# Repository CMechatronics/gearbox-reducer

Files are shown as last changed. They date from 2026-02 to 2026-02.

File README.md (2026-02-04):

# Industrial Gearbox Speed Reducer

## Overview
This project presents the **design and analysis of an industrial spur gear speed reducer** intended for continuous operation in an automated system.  
The gearbox is designed to reduce motor speed while increasing output torque, ensuring safe and reliable operation.

  ## Technical Specifications
- **Input power:** 7.5 HP  
- **Input speed:** 1440 rpm  
- **Transmission ratio:** i = 2.034 : 1  
- **Output speed:** ≈ 708 rpm  
- **Output torque:** 7.5 kgf·m  
- **Gear type:** Spur gears (straight teeth)  
- **Safety factor:** 3  
- **Lubrication:** Oil bath  
- **Expected service life:**  
  15 years – 300 working days/year – 16 h/day

## Design Scope
The project includes:
- Mechanical design of shafts, gears, housing, and auxiliary components  
- Strength and fatigue calculations for:
  - Gears  
  - Shafts  
  - Keys  
  - Bearings  
- Selection of standard components (bearings, seals, fasteners)  
- Compliance with applicable industrial and safety regulations  
- Manufacturing-oriented drawings and bill of materials  

## Repository Structure
- **/docs** – Design report, calculations, specifications, and budget  
- **/drawings** – Assembly and part drawings  
- **/cad** – 3D CAD models (STEP and native files)  
- **/analysis** – Calculation breakdown by component  
- **/references** – Standards and technical references  

## Tools & Standards
- CAD modeling (mechanical design)  
- Analytical calculations based on mechanical design theory  
- Reference to UNE / EN industrial standards where applicable  

## Author
Carlos López Jiménez  
Industrial Mechatronics – Mechanical Design Project  

## Disclaimer
This repository contains an **engineering design project** developed for technical and educational purposes.  
It is not intended for direct industrial manufacturing without further validation.

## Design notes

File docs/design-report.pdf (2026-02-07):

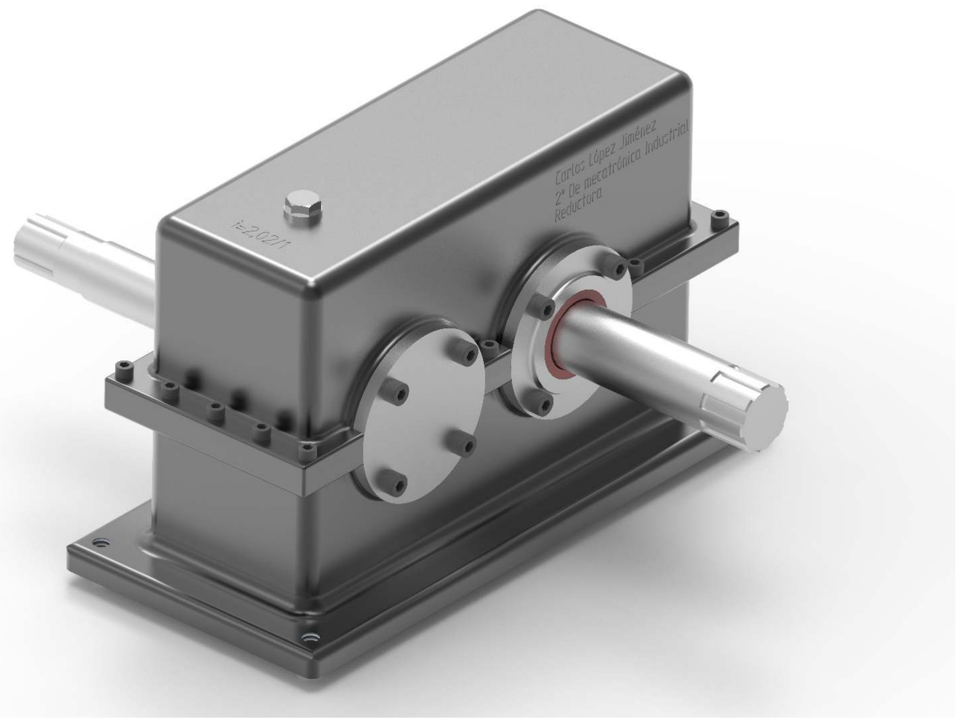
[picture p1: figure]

# PROYECTO REDUCTORA

### DOCUMENTO COMPLETO

CARLOS LÓPEZ JIMÉNEZ
2º DE MECATRÓNICA INDUSTRIAL Salesianos San Ignacio Cádiz

## 21 DE FEBRERO DE 2022

PROYECTO REDUCTORA | 21 DE FEBRERO DE 2022
CARLOS LÓPEZ JIMÉNEZ | 1

Índice general

Memoria del proyecto | 2
Presupuesto | 15
Pliego de condiciones | 48
Planos | 62
Anexo Cálculos | 76

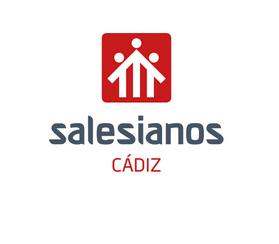
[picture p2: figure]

CARLOS LÓPEZ JIMÉNEZ 2

# Proyecto Reductora de velocidad por engranajes

2º de Mecatrónica Industrial.

# Documento Nº1:

# Memoria del proyecto

Código PR-1

Autor: Carlos López Jiménez Fecha: 21/02/2022

CARLOS LÓPEZ JIMÉNEZ 3

# Índice

2.1.3.1.1 Reducción de velocidad del motor eléctrico mediante variadores de frecuencia. . 4

### 2.1.3.1.2. Reducción de velocidad del motor mediante reductora de velocidad de

### 2.1.3.1.3 Reducción de velocidad del motor mediante reductora de velocidad de tornillo

CARLOS LÓPEZ JIMÉNEZ 4

2.1Principios del documento

Código identificativo: PR-1

2.1.1 Antecendentes del proyecto.

El peticionario José Fuentes Macías con C.I.F. nº: B-12.432.654, y domicilio social en Avenida de la corte 43, 2º izquierda de la localidad de Marbella, Málaga. Posee en Avenida del Polígono Nave 32 de la localidad de Rota, Cádiz, una nave o local donde pretende instalar una actividad dedicada a automatizar la gestión de artículos / Paletizador de velocidad estable.

Se redacta el presente proyecto por el Ingeniero Mecatrónico, Javier González, colegiado en el Colegio oficial de Ingenieros Técnicos Industriales de Aragón con el número 1287.

2.1.2 Objeto del presente proyecto.

Se pretende con este proyecto describir la máquina que desea realizar, justificando y valorando cada una de las partes que componen esta máquina, a fin de recabar de los organismos competentes las oportunas autorizaciones que permitan su legalización y puesta en marcha. La finalidad de dicho proyecto se resume en reducir la velocidad de entrada del brazo mecánico “n” veces para que este trabaje a una adecuada velocidad sin producir riesgos.

2.1.3 Soluciones adoptadas.

2.1.3.1 Soluciones alternativas.

Las soluciones alternativas a las necesidades del cliente son las siguientes:

1. Reducción de velocidad del motor eléctrico mediante variadores de frecuencia.

### 2. Reducción de velocidad del motor mediante reductora de velocidad de

engranajes rectos.

### 3. Reducción de velocidad del motor mediante reductora de velocidad de tornillo

sin fin y corona.
4. Reducción de velocidad del motor mediante reductores planetarios.

2.1.3.1.1 Reducción de velocidad del motor eléctrico mediante variadores de frecuencia.

Descripción del elemento:

CARLOS LÓPEZ JIMÉNEZ 5

Este elemento varía la velocidad gracias a la tecnología electrónica, variando la frecuencia suministrada al motor se puede conseguir que este varíe de velocidad.

La reducción de velocidad del motor por este método puede llegar a ser acertada si el coste de la instalación de este elemento fuera el de un variador de gama baja, es decir en torno a unos 100-500 euros.
La causa de no elegir esta opción es por el simple hecho de que el consumo para el que está diseñado este no es superior al demandado por ello el variador terminaría dañado. Esta potencia que necesitamos es debido a la gran carga que se le quiere dar al paletizador.

Coste económico:

Las opciones de gama alta solucionarían el problema del consumo, pero no el del coste ya que estos rondan sobre los 1600 – 3000 Euros.

Límite tecnológico:

Esta opción como límite tecnológico tiene el problema de que la red eléctrica debe ser cuidada, existe el problema de la generación de ruido por las conmutaciones de los transistores del variador, por ello en este tipo de instalaciones se debe instalar un filtro para no perturbar la señal eléctrica de las demás redes, esto trae los siguientes problemas:

- Mantenimiento de la red eléctrica.
- Instalación del cuadro general de mando y protección dedicado al motor y a su variador.
- Posibles perturbaciones eléctricas en la instalación del emplazamiento e incluso llegando a poder a afectar a otros emplazamientos.
- Costes de instalación caros (filtros, adecuación de instalación del circuito para el motor y el variador).

Como oportunidades para este elemento tenemos las siguientes:

- Puede ser una buena oportunidad para realizar una correcta instalación eléctrica de la nave.
- Una vez realizado los cambios el variador puede limitar el posible exceso de velocidad del motor.
- Los variadores de alta gama protegen a los motores de una forma eficiente.
- Ahorro del consumo del motor entorno a un 20-70%.

Como impacto visual o estético y medioambiental:

La instalación debe ser adecuada y deberá estudiarse la manera de colocar el subcuadro de protección para este instrumento y para la línea trifásica del motor. Por

CARLOS LÓPEZ JIMÉNEZ 6

su reducción de consumo mejora el impacto medioambiental que hubiera generado sin el variador.

Según lo permitido por las administraciones y normativas legales este instrumento es valido para las instalaciones dentro de España según la directiva de la UE 2011/65/UE y 2015/863.

2.1.3.1.2 Reducción de velocidad del motor mediante reductora de velocidad de engranajes rectos.
Descripción del elemento:

La reductora de velocidad de engranajes rectos está formada por pares de ruedas que pueden ser de cualquier tipo, es decir, de dientes rectos, helicoidales, grupos cónicos, etc...

Coste económico:

El coste económico de este tipo de reductores de velocidad puede llegar a ser entre los 1000-1500 euros, en esto se tiene en cuenta la fabricación de estos ya que es para una relación de transmisión personalizada para así poder con la carga que se le dé al paletizador

Límite tecnológico:

En este aspecto tenemos un claro límite en el par o torque, los engranajes, los árboles y las chavetas serán los elementos claramente recibirán los esfuerzos demandados, por ello hay que tener muy claro cual va a ser la masa máxima a soportar con un límite de seguridad. Por otra parte, se enfrentan a otros problemas como pueden ser:

- Mantenimiento de la reductora (revisión del aceite, revisión de las ruedas, árboles y chavetas).
- Limitaciones de carga (estudiar las cargas).
- Tener en cuenta las condiciones del ambiente (temperatura, humedad…).
- Fabricación de piezas (tiempos de espera de la fabricación hasta obtener el producto).
- Revisar el sitio donde se situará la reductora y fijarla (Realizar una buena instalación).
- Si se estropea habría que volver a encargar las piezas, el plazo puede ser largo pudiendo aumentar la criticidad de producción de la empresa por inutilización del paletizador.

Como oportunidades para este elemento tenemos las siguientes:

- Si se diseña bien el conjunto puede tener una gran vida útil.
- Como la lubricación es un tipo de lubricación automática si esta no pierde aceite no será necesario un mantenimiento exhaustivo.

CARLOS LÓPEZ JIMÉNEZ 7

- Tamaño compacto.
- Instalación rápida.
- Ofrece una buena seguridad en la transmisión.

Como impacto visual o estético y medioambiental:

El impacto visual es muy reducido ya que el equipo es compacto. Para reducir el impacto medioambiental del aceite mineral deberá llevarse a contenedores específicos para ello.

Este elemento deberá seguir la norma UNE-EN 13463-6:2005 por la peligrosidad del aceite como fuente de ignición (en su estado gaseoso puede generarse una reacción química con el oxígeno que lo convierta en inflamable).

2.1.3.1.3 Reducción de velocidad del motor mediante reductora de velocidad de tornillo sin fin y corona.
Descripción del elemento:

El mecanismo consiste en un tornillo sinfín montado en el eje motor haciendo girar la corona en el que estará fijado solidariamente el eje de salida, por transmisión de fuerza y movimiento entre estos ejes son capaces de resistir cargas muy elevadas.

Coste económico:

En cuanto al coste económico debemos tener en cuenta que se trata de un elemento que al igual que la reductora deberán de fabricarse las piezas del conjunto, teniendo en cuenta la dificultad de fabricación del tornillo sinfín y que por ello la forma de los dientes de la corona será más compleja que la de los dientes rectos puede llegar a ser más laborioso, por ello los costes podrían ascender a unos 2000-2600 euros.

Límite tecnológico:

Como límite tecnológico tenemos que por lo general no se puede realizar un cambio de entrada de transmisión ya que el sinfín es el que se suele usar para transmitir el movimiento al árbol motriz. Pueden existir otros problemas como:

- Si no se diseña correctamente y aparece un fallo repentino este no podrá ser sustituido con brevedad ya que se deberá fabricar de nuevo
- Una de las principales desventajas del sinfín es el bajo rendimiento que ofrecen estas etapas de reducción, que puede situarse en torno al 15% debido a los altos valores de fuerza de rozamiento y a los esfuerzos axiales asociados.

CARLOS LÓPEZ JIMÉNEZ 8

- El desgaste que sufre el sinfín se produce en las superficies de apoyo las cuales están sometidas a fricción, por ello es necesario que sean altamente resistentes y que estén perfectamente calibrados para que su vida útil sea larga.
- Existe un cierto riesgo de desgaste de los filetes si se produce fricción excesiva en la zona.

Como oportunidades para este elemento tenemos las siguientes:

- Tamaño compacto
- Si se diseña correctamente puede tener una larga vida útil.
- Poco mantenimiento ya que su lubricación es automática.

Como impacto visual o estético y medioambiental:

No perturba la visión estética ya que es un elemento compacto, pero con su aceite mineral se deberá cuidar su correcto reciclado.

Este elemento deberá seguir la norma UNE-EN 13463-6:2005 por la peligrosidad del aceite como fuente de ignición (en su estado gaseoso puede generarse una reacción química con el oxígeno que lo convierta en inflamable).

2.1.3.1.4 Reducción de velocidad del motor mediante reductores planetarios. Descripción del elemento:

Los reductores planetarios se caracterizan por un elevado grado de efectividad y, gracias a su forma de construcción compacta, ofrece una alta densidad de potencia en comparación con otros tipos de construcción de reductores. Especialmente la utilización de una rueda hueca reduce tanto el volumen como la masa de este tipo de reductor.

Coste económico:

Los costes de estos engranajes son muy costosos, el diseño puede llegar a ser complejo y su fabricación también lo es, por ello los costes pueden ascender a los 200-4000 euros si se requiere un buen par de fuerza en torno a los 400 Nm.

Límite tecnológico:

No se pueden hacer más silenciosos, y sin lubricante no podrán funcionar correctamente. Otros inconvenientes pueden ser:

- El engranaje debe ser preciso para asegurar el reparto de la carga

CARLOS LÓPEZ JIMÉNEZ 9

- Las elevadas cargas de los cojinetes pueden provocar un descaste prematuro en la construcción de muñones.
- Generalmente necesita lubricación con grasa, pero la lubricación de baño en aceite es mejor
- Relación alta de longitud a diámetro cuando se utilizan múltiples etapas (el reductor se vuelve muy largo).
- Alto costo

Como oportunidades para este elemento tenemos las siguientes:

Este se puede útil por su eficiencia, en ese aspecto cumpliría por encima las expectativas, así como su ligereza. También se pueden resaltar las siguientes características:

- Tamaño compacto y bajo peso hasta un 50 % de reducción con el mismo par de torsión
- Densidad de alta potencia
- Vida larga de los engranajes
- Muy preciso
- Etapas modulares, más planetarias pueden ser apiladas.

Como impacto visual o estético y medioambiental:

En este caso este tipo de reductora si crea un impacto visual y puede romper con la estética ya debido a la cantidad de etapas esta reductora termina siendo alargada y ocupando espacio quedando vistoso a simple vista. Hay que tener en cuenta que el aceite deberá ser correctamente reciclado.

Este elemento deberá seguir la norma UNE-EN 13463-6:2005 por la peligrosidad del aceite como fuente de ignición (en su estado gaseoso puede generarse una reacción química con el oxígeno que lo convierta en inflamable).

2.1.3.2 Justificación de la solución adoptada.
Reuniendo las características de las cuatro opciones plantadas se ha llegado a una conclusión de que la mejor opción en términos de calidad es la reductora de velocidad de engranajes rectos.

Comparando esta opción con las demás consideramos que es la mejor opción por las siguientes características que resaltan respecto a los demás:

- Elemento compacto
- Poco vistoso
- Fabricación del conjunto relativamente simple respecto a los demás, exceptuando al variador.

CARLOS LÓPEZ JIMÉNEZ 10

- Si bien es verdad que este tipo de reductora no está pensada para cargas muy grandes el cliente especifica que no es necesario que en ese aspecto resalte tanto como por ejemplo la reductora con sinfín y corona, que si están pensados para esfuerzos muy grandes, concretamente por la función que desempeñará no tendrá que soportar la carga completa de la carga máxima permitida en cuestión
- La instalación es muy sencilla y por ello podemos evitar reducir la cantidad de instalaciones adicionales como ocurre en el caso del variador de frecuencia.
- En tema legislativo no es complejo, es mínimo, como ocurre con el caso del aceite.
- Económicamente se adapta al presupuesto máximo que se permite gastar el cliente.
2.1.4. Reglamentaciones y disposiciones oficiales particulares.
Se redacta el presente proyecto para dar cumplimiento a las siguientes:
- Esta reductora cumple con la directiva europea 94/9/CE (ATEX-100) Real Decreto 400/1996 con temática para aparatos y sistemas de protección para usos en atmósferas explosivas.
- El lugar donde se instalará cumple con la directiva europea 99/92/CE (ATEX-
137) Real Decreto 681/2003 con temática de protección de la seguridad y salud de los trabajadores expuestos a los riegos derivados de la presencia de atmósferas explosivas en el lugar de trabajo.
- Esta reductora no debe instalarse en un emplazamiento en el que el ambiente sea potencialmente explosivo por precaución. Las mezclas de gas explosivas o concentraciones de polvo pueden causar graves daños en combinación con partes calientes en movimiento de los reductores.
- La instalación, conexión, puesta en marcha y tareas de mantenimiento o reparación de los reductores deberán ser efectuadas únicamente por técnicos cualificados.
- Este reductor estándar no puede utilizarse en entornos con una atmósfera potencialmente explosiva. Para dicho uso debe solicitarse la ejecución específica que satisfaga la directiva 94/9/CE (ATEX).
- Este reductor está destinado a ser incorporado y/o ensamblado con otras máquinas o componentes, se considera “componente·, por lo que no puede ponerse en servicio antes de que la máquina a la que se va a incorporar se declare conforme a las disposiciones de la directiva de máquinas 2006/42/CE.
- Real Decreto 786/2001, de 6 de Julio, por el que se aprueba el reglamento de seguridad contra incendios en establecimientos industriales.
- NBE CPI-96 de Protección contra Incendios en los Edificios
- Reglamento de Actividades Molestas, Insalubres, Nocivas y peligrosas (Decreto 241461 de 3/11/61).

CARLOS LÓPEZ JIMÉNEZ 11

- Decreto 297/1995 de 19 de Diciembre (Boja nº3/11-01-96) por el que se aprueba el reglamento de Calificación Ambiental.
- Real Decreto 1435/92 por el que se dictan las disposiciones de aplicación de la directiva del Concejo 89/92/CEE, relativa a la aproximación de las legislaciones de los estados miembros sobre máquinas.

2.1.4.1 Bibliografía
Normativas usadas para la reductora:

http://rodytrans.es/wp-content/uploads/Manual-instrucción-montaje-engranajes.pdf

http://www.atmosferasexplosivas.com/index.php/normativaatex

Reductores de velocidad:

https://clr.es/blog/es/reductores-velocidad-funcionamiento/

https://www.nord.com/es/productos/reductores-industriales/motorreductores_industriales.jsp;jsessionid=DECCDB9545F884C51F9605EBA068EC99?missing=/cms/es/product_catalogue/industrial_gear_unit/pgop_industrial_gear_unit_1.jsp

Variadores de frecuencia:

https://new.abb.com/drives/es/que-es-un-variador

2.1.4.2 Plan de gestión de la calidad aplicado durante la redacción del proyecto. Se han asegurado los procesos de calidad correspondientes a la fabricación de la reductora estos son los descritos a continuación:

- Planificación de la fabricación y definir procesos.
- Planificación del montaje
- Distribución del trabajo.
- Evaluación de riesgos.
- Medidas de prevención de riesgos.
- Hoja de recopilación de datos
- Histograma
- Diagrama de dispersión
- Gráficos de control
- Mantenimiento productivo total (TPM)

CARLOS LÓPEZ JIMÉNEZ 12

2.1.5 Requisitos de diseño
En este proyecto el cliente facilita los datos de partida requeridos que son los descritos en la siguiente tabla:

Condiciones expuestas por el cliente
P (CV) | 7,5
n (rpm) | 1440
Par de salida (Kgf·m) | 7,5
Factor de seguridad (S) | 3
Vida útil | 15 años, 300 días laborables y 16 h/día de trabajo

El cliente solicita una reductora de engranajes de dientes rectos, en el de base tenemos que la potencia en Caballos de Vapor es de 7,5 a su vez determina que la velocidad del motor en revoluciones por minuto será de 1440.
Le preocupa que el par de salida sea inferior a 7,5 y superior a 8 Kilogramos fuerza por metro.
Determinamos un factor de seguridad de 3 para los elementos que serán sometidos a esfuerzos.

Al cliente le preocupa que la vida útil sea de la reductora sea inferior a 15 años, 300 días laborables y 16 h/día de trabajo.

2.1.5.1 Legislación, reglamentación y normativas aplicables.
Estas se han señalado en el apartado de 2.1.4 Normas y referencias.

2.1.5.2 Estudios realizados encaminados a la definición de la solución adoptada.
En la reductora elegida según el apartado 2.1.3 Solución adoptada, se refleja el por qué se ha decidido realizar el diseño de la reductora en concreto.
En este apartado se señalarán las decisiones de construcción de elementos adoptadas.

En la mayoría de los apartados siguientes se reflejó la justificación de elección en el Anexo de Cálculos, por ello los apartados que no estén explicados en dicho anexo serán justificados aquí.

2.1.5.2.1 Árboles de transmisión
En esta reductora se ha elegido reducción de velocidad por 2 pares de ruedas, lo que conlleva a que existan 2 árboles, uno conductor y otro conducido.

En el Anexo de Cálculos apartado 1.4 se refleja la elección de los árboles de diámetro

### 35 y 40 según el momento flector dado en cada uno de ellos y considerando el tamaño

más reducido posible para obtener un tamaño compacto de la reductora.

CARLOS LÓPEZ JIMÉNEZ 13

2.1.5.2.2 Ruedas dentadas.
El piñón y la corona son dos elementos esenciales, se decidió una transmisión con ruedas de dientes rectos en el apartado 2.1.3 Solución adoptada. Se ha determinado las dimensiones tendiendo a reducir el volumen de estas al máximo posible atendiendo también a obtener el par de fuerza acordado. Los detalles aparecerán en el Anexo de Cálculos apartado 1.3

2.1.5.2.3 Chavetas.
Las chavetas elegidas han sido elegidas según el esfuerzo calculado al que se verán sometidas, a partir de estos datos se ha elegido una longitud de chaveta acorde a la superficie del chavetero siendo esta de largo inferior a la longitud de dicho chavetero, de este modo se ha atendido al catálogo del fabricante norelem mirando que cumpla las expectativas calculadas.

Más información referenciada en Anexo de Cálculos apartado 1.5

2.1.5.2.4 Rodamientos.
Los rodamientos para carga radial son elegidos según la carga a las que son sometidos, se ha escogido al fabricante de rodamientos SKF donde en el anexo de cálculos en los que se puede observar que según la carga que se ha determinado estos son aptos para este conjunto.

Más información referenciada en el Anexo de Cálculos apartado 1.6

2.1.5.2.5 Retenes
Los retenes elegidos han sido unos NBR (caucho de Acrilo nitrilo butadieno), en dimensiones nos hemos ceñido a la menor dimensión posible de su diámetro exterior, su diámetro interior atendiendo a el árbol de transmisión respectivo.

Elección aclarada en el Anexo de Cálculos apartado 1.8

2.1.5.2.6 Elementos de montaje.
Todos los elementos de montaje tales como la carcasa, tapetas, casquillos y tornillos han sido elegidos con el enfoque de obtener una reductora lo más compacta posible, por ello se han determinado dimensiones lo más reducidas posibles pero que también aporten un acople entre estos.

Más información en el Anexo de Cálculos apartado 1.9 donde se aclara el diseño geométrico de los distintos elementos constructivos.

2.1.5.2.7 Lubricación
La lubricación es un factor muy importante donde exista rozamiento entre piezas, se puede alargar la vida útil de este, así como el rendimiento seleccionando un buen lubricante.

Se ha optado por realizar un baño en aceite ya que es el más adecuado para este caso ya que las propias ruedas serán la que se impregnen continuamente de aceite

CARLOS LÓPEZ JIMÉNEZ 14

teniendo una lubricación óptima en todo momento. En el Anexo de Cálculos apartado 1.7.

2.1.6 Resultados finales.
Como se ha ido viendo según los pasos dados hemos obtenido una reductora de velocidad por 2 pares de engranajes rectos cuales son fijados gracias a sus chaveteros que se acoplarán con los chaveteros de los árboles de transmisión, el movimiento axial será limitado gracias a los casquillos separadores que harán tope con los rodamientos y estos a su vez con la tapeta que estará fijada a la carcasa. Esta reductora dispondrá de un tapón de llenado y de vaciado para obtener una lubricación automática, en pocas palabras obtendremos un reductor de velocidad compacto y simple ya que solo existe una sola etapa, este podrá ser fijado gracias a los orificios pasantes que se han facilitado en cada esquina de la reductora.

La transmisión de movimiento entre el motor y el árbol de transmisión se realizará mediante un acople de ejes con acanaladuras.

2.1.7 Planificación.
En este proceso de fabricación de la reductora se han tenido diferentes etapas, se definirán a continuación:
- Etapa de replanteo y planificación: Se examinaron los datos solicitados por el cliente desde el departamento de administración, se pasaron los datos al departamento técnico que estudió las peticiones del cliente y en este se planificó la forma de en la que se iba a hacer.
- Etapa de estudio y desarrollo: Se finalizó el estudio completo de las posibilidades que se plantearon y se comenzó el desarrollo una vez establecido una comunicación con el cliente. Se desarrollaron los cálculos necesarios y los planos de los elementos una vez determinados.
- Etapa de estimación de tiempo de entrega y fabricación: Una vez terminado el estudio y la realización de planos se estimó el tiempo de fabricación, empaquetado y envío y se realizó un presupuesto completo, se le pidió al cliente una confirmación de este, una vez recibida la señal se inició la fabricación con las fechas de entrega asignadas.
2.1.8. Orden de prioridad entre los documentos básicos.
Orden de documentos básicos:

1 Planos.
2 Pliego de condiciones.
3 Presupuesto.
4 Memoria.

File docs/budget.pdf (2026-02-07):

PROYECTO REDUCTORA | 21 DE FEBRERO DE 2022


CARLOS LÓPEZ JIMÉNEZ | 15

# Proyecto Reductora de velocidad por engranajes

2º de Mecatrónica Industrial.

# Documento Nº4:

# Presupuesto

Código PR-4

Autor: Carlos López Jiménez Fecha: 21/02/2022

Presupuesto | Reductora
Mediciones | Reductora
Capítulo | 01
Código | Ud | N | Long | Ancho | Altura

Cantidad
Precio Importe

### 01.0 Piñón

Ud Piñón | 1 | 69 | ø 85,25
Total: | 1

### 01.1 Corona

Ud Corona | 1 | 69 | ø 167,75
Total: | 1

### 01.2.0 Árbol de transmisión de entrada

Ud Árbol de entrada | 1 | 267 | ø 35
Total: | 1

### 01.2.1 Árbole de transmisión de salida

Ud Árbol de salida | 1 | 267 | ø 40
Total: | 1

### 01.3.1 Tapeta árbol de entrada

Ud Tapeta árbol de entrada | 1 | 16 ø 100
Total: | 1

### 01.3.2 Tapeta árbol de entrada ciega

Ud Tapeta árbol de entrada ciega | 1 | 13 ø 100
Total: | 1

### 01.3.3 Tapeta de árbol de salida

Ud Tapeta árbol de salida | 1 | 16 ø 100
Total: | 1

Subcapítulo

Subcapítulo

Reductora

Descripción

Subcapítulo

Subcapítulo

Subcapítulo

Ruedas dentadas

Árboles de transmisión

Tapetas

Subcapítulo

Subcapítulo

Carlos López Jiménez | 21/02/2021 | Página 1

Mediciones | Reductora
Capítulo | 01
Código | Ud | N | Long | Ancho | Altura

Cantidad
Precio Importe

Reductora

Descripción

### 01.3.4 Tapeta árbol de salida ciega

Ud Tapeta árbol de salida ciega | 1 | 13 ø 100
Total: | 1

### 01.4.0 Casquillos separadores árbol de entrada

Ud Casquillo separador árbol de entrada | 2 | 15 ø 45
Total: | 2

### 01.4.1 Casquillos separadores árbol de salida

Ud Casquillo separador árbol de salida | 2 | 15 ø 50
Total: | 2

### 01.5.0 Caja de la reductora parte inferior

Ud Caja de de reductora parte inferior | 1 | 380 | 179 110,5
Total: | 1

### 01.5.1 Caja de la reductora parte superior

Ud Caja de reductora parte superior | 1 | 358 | 117 106,5
Total: | 1

### 01.6.0 Tornillería

Ud Tornillo M6 x 18 | 14 | 18 | | ø 6
Ud Tornillo M8 x 16 | 16 | 16 | | ø 8
Ud Tornillo tapón M16 x 12 | 2 | 12 | | ø 16
Total: | 32

### 01.6.1 Elementos de arrastre

Ud Lengüeta plana tipo A 12x8x56 | 1 | 12 | 56 | 8
Ud Lengüeta plana tipo A 10x8x56 | 1 | 10 | 56 | 8

Subcapítulo

Subcapítulo

Elementos que no se tienen que fabricar

Subcapítulo

Subcapítulo

Subcapítulo

Casquillos

Caja

Subcapítulo

Subcapítulo

Carlos López Jiménez | 21/02/2021 | Página 2

Mediciones | Reductora
Capítulo | 01
Código | Ud | N | Long | Ancho | Altura

Cantidad
Precio Importe

Reductora

Descripción

Total: 2

### 01.6.2 Rodamientos

Ud Rodamientos rígidos de bolas 16007 | 2 | 9 ø 62
Ud Rodamientos rígidos de bolas 16008 | 2 | 9 ø 68
Total: | 4

### 01.6.3 Retenes

Ud Retén NBR 35x45x7 | 2
Ud Retén NBR 40x52x7 | 2
Total: | 4

### 01.6.4 Elementos consumibles

l | 2,85
gr | 110

2,85

110

### 01.7.0 Montaje

Ud Montaje | 1
Total: | 1

Subcapítulo

Montaje

Sellador para estanqueidad de uniones

Lubricante API GL1

Total litros:

Total gramos:

Subcapítulo

Subcapítulo

Subcapítulo

Carlos López Jiménez | 21/02/2021 | Página 3

Procesos descompuestos | Reductora
Capítulo | 01
Código | Ud

N

Tiempo total
de la
operación

Precio
unidad Importe

### 01.1.0 Piñón

Ud

Kg | Cilindro Acero 37Cr4 | 1 | 5 | | 7,50 € | 37,50 €
minutos | Estudiar plano y hoja de proceso | 1 | 2 | 2 | 0,33 € | 0,66 €
minutos | Recoger , limpiar y devolver piezas útiles | 3 | 5,11 | 15,33 | 0,33 € | 5,06 €
minutos | Limpieza de la máquina | 1 | 15 | 15 | 0,33 € | 4,95 €
minutos | Puesta a punto ejes X y Z comprobaciones y control | 1 | 4,8 | 4,8 | 0,33 € | 1,58 €
minutos | Coger trozo de material, posicionarlo, centrar a mano y quitar | 1 | 0,7 | 0,7 | 0,33 € | 0,23 €
minutos | Poner ajustar y quitar pinza con soporte cónico autocentrante | 3 | 0,7 | 2,1 | 0,33 € | 0,69 €
minutos | Montar, centrar/ ajustar y desmontar herramienta o portaherramienta de acabado | 1 | 0,85 | 0,85 | 0,33 € | 0,28 €
minutos | Montar herramienta en portaherramientas | 1 | 0,25 | 0,25 | 0,33 € | 0,08 €
minutos | Ajustar altura de la cuchilla | 1 | 0,42 | 0,42 | 0,33 € | 0,14 €
minutos | Comprobar alineación puntros eje y contracabezal con barra de prueba y comparador centesimal | 2 | 5 | 10 | 0,33 € | 3,31 €
minutos | Cambio de herramienta | 1 | 0,35 | 0,35 | 0,33 € | 0,12 €
minutos | Colocación del carro en posición de trabajo, ajustar pasada y aproximar herramienta a la pieza | 6 | 0,55 | 3,3 | 0,33 € | 1,09 €
minutos | Primera pasada de prueba, medir y volver a posición de trabajo | 2 | 0,15 | 0,3 | 0,33 € | 0,10 €
minutos | Sacar y volver a introducir la herramienta para eliminar viruta | 6 | 0,15 | 0,9 | 0,33 € | 0,30 €
minutos | Retirar carro, ajustar pasada con el nonio y volver a posición de trabajo | 6 | 0,55 | 3,3 | 0,33 € | 1,09 €
minutos | Comprobación de medidas | 2 | 0,3 | 0,6 | 0,33 € | 0,20 €
minutos | Comprobación medida final | 1 | 0,3 | 0,3 | 0,33 € | 0,10 €
minutos | Invertir pieza amarrada en plato universal | 2 | 0,3 | 0,6 | 0,33 € | 0,20 €

Reductora

Descripción

Cantidad (Kg o
min)

Ruedas dentadas

Fabricación de piñón según planos al que se le hará un chavetero acorde a la lengüeta designada, las operaciones se realizarán mediante fresas para el mecanizado y tallado de dientes. Material empleado: 37Cr4

Subcapítulo

Carlos López Jiménez | 21/02/2021 | 25

Capítulo | 01
Código | Ud

N

Tiempo total
de la
operación

Precio
unidad Importe

Reductora

Descripción

Cantidad (Kg o
min)
minutos | Colocación de fresa | 1 | 0,55 | 0,55 | 0,33 € | 0,18 €
minutos | Colocación de rueda dentada en el plato universal | 1 | 0,4 | 0,4 | 0,33 € | 0,13 €
minutos | Ajuste de aparato divisor | 1 | 5 | 5 | 0,33 € | 1,65 €
minutos | Tallado de un diente | 29 | 1,5 | 43,5 | 0,33 € | 14,39 €
minutos | Taladrado ø35 H7 | 1 | 4 | 4 | 0,33 € | 1,32 €
minutos | Fresado del chavetero 69 mm longitud y 3,3 mm de t2 | 1 | 1,2 | 1,2 | 0,33 € | 0,40 €
minutos | Refrentado de 1 mm para llegar a 15 mm, hacer en las dos caras | 30 | 0,5 | 15 | 0,33 € | 4,96 €
minutos | Cilindrado de 1mm para vaciado de rueda desde ø62 a ø45 (17 mm de cilindrado) hacer en las dos caras | 34 | 0,4 | 13,6 | 0,33 € | 4,50 €
Tiempo total invertido en minutos | 144,35
Ud | horas
| 2,406
MO01 | horas | Oficial de 1ª Ferralista | 1 | 19,85 € | 47,76 €
| | | Subtotal partida subcapítulo 01.1 (CD) | | 85,26 €
| | | %Costes Indirectos (CI) | | 7%
| | | Total partida subcapítulo 01.1 | | 91,22 €
| | 01.1.1 Corona
| Ud
Kg | Cilindro Acero 37Cr4 | 1 | 20 | | 7,50 € | 150,00 €
minutos | Estudiar plano y hoja de proceso | 1 | 2 | 2 | 0,33 € | 0,66 €
minutos | Recoger , limpiar y devolver piezas útiles | 3 | 5,11 | 15,33 | 0,33 € | 5,06 €
minutos | Limpieza de la máquina | 1 | 15 | 15 | 0,33 € | 4,95 €
minutos | Puesta a punto ejes X y Z comprobaciones y control | 1 | 4,8 | 4,8 | 0,33 € | 1,58 €
minutos | Coger trozo de material, posicionarlo, centrar a mano y quitar | 1 | 0,7 | 0,7 | 0,33 € | 0,23 €
minutos | Poner ajustar y quitar pinza con soporte cónico autocentrante | 3 | 0,7 | 2,1 | 0,33 € | 0,69 €
minutos | Montar, centrar/ ajustar y desmontar herramienta o portaherramienta de acabado | 1 | 0,85 | 0,85 | 0,33 € | 0,28 €
minutos | Montar herramienta en portaherramientas | 1 | 0,25 | 0,25 | 0,33 € | 0,08 €
minutos | | 1 | 0,42 | 0,42 | 0,33 € | 0,14 € Ajustar altura de la cuchilla

Fabricación de piñón según planos al que se le hará un chavetero acorde a la lengüeta designada, las operaciones se realizarán mediante fresas para el mecanizado y tallado de dientes. Material empleado: 37Cr4

Subcapítulo

Capítulo | 01
Código | Ud

N

Tiempo total
de la
operación

Precio
unidad Importe

Reductora

Descripción

Cantidad (Kg o
min)
minutos | Comprobar alineación puntros eje y contracabezal con barra de prueba y comparador centesimal | 2 | 5 | 10 | 0,33 € | 3,31 €
minutos | Cambio de herramienta | 1 | 0,35 | 0,35 | 0,33 € | 0,12 €
minutos | Colocación del carro en posición de trabajo, ajustar pasada y aproximar herramienta a la pieza | 6 | 0,55 | 3,3 | 0,33 € | 1,09 €
minutos | Primera pasada de prueba, medir y volver a posición de trabajo | 2 | 0,15 | 0,3 | 0,33 € | 0,10 €
minutos | Sacar y volver a introducir la herramienta para eliminar viruta | 6 | 0,15 | 0,9 | 0,33 € | 0,30 €
minutos | Retirar carro, ajustar pasada con el nonio y volver a posición de trabajo | 6 | 0,55 | 3,3 | 0,33 € | 1,09 €
minutos | Comprobación de medidas | 2 | 0,3 | 0,6 | 0,33 € | 0,20 €
minutos | Comprobación medida final | 1 | 0,3 | 0,3 | 0,33 € | 0,10 €
minutos | Invertir pieza amarrada en plato universal | 2 | 0,3 | 0,6 | 0,33 € | 0,20 €
minutos | Colocación de fresa | 1 | 0,55 | 0,55 | 0,33 € | 0,18 €
minutos | Colocación de rueda dentada en el plato universal | 1 | 0,4 | 0,4 | 0,33 € | 0,13 €
minutos | Ajuste de aparato divisor | 1 | 5 | 5 | 0,33 € | 1,65 €
minutos | Tallado de un diente | 59 | 1,5 | 88,5 | 0,33 € | 29,28 €
minutos | Taladrado ø40 H7 | 1 | 4 | 4 | 0,33 € | 1,32 €
minutos | 3,3 mm de t2 | 1 | 1,2 Fresado del chavetero 69 mm longitud y | 1,2 | 0,33 € | 0,40 €
minutos | hacer en las dos caras | 30 | 0,5 Refrentado de 1 mm para llegar a 15 mm, | 15 | 0,33 € | 4,96 €
minutos | Cilindrado de 1mm para vaciado de rueda desde ø140 a ø50 (90 mm de cilindrado) hacer en las dos caras | 180 | 0,4 | 72 | 0,33 € | 23,82 €
Tiempo total invertido en minutos | 247,75
Ud | horas
| 4,129
MO01 | horas | Oficial de 1ª Ferralista | 1 | 19,85 € | 81,96 €
Subtotal partida subcapítulo 01.1.1 (CD) | 231,96 €
| | | %Costes Indirectos (CI) | | 7%
| | | Total partida subcapítulo 01.1.1
| | | Total partida subcapítulo 01.1 | | 339,43 €

### 01.2.0 Árbol de transmisión de entrada

Ud

Árboles de transmisión

Subcapítulo

Fabricación del árbol de transmisión de entrada de 267 mm de largo, Ø35 h11, fabricación asiento para la lengûeta plana de 10x8x56, achaflanado de extremos del árbol y fabricación en un extremo de nervado de longitud 30 y Ø32. Material empleado: Acero 37CrMo4

248,2014 €

Capítulo | 01
Código | Ud

N

Tiempo total
de la
operación

Precio
unidad Importe

Reductora

Descripción

Cantidad (Kg o
min)
Kg | Cilindro Acero 37CrMo4 | 1 | 3,7 | | 6,70 € | 24,79 €
minutos | Estudiar plano y hoja de proceso | 1 | 2 | 2 | 0,33 € | 0,66 €
minutos | Recoger , limpiar y devolver piezas útiles | 3 | 5,11 | 15,33 | 0,33 € | 5,06 €
minutos | Limpieza de la máquina | 1 | 15 | 15 | 0,33 € | 4,95 €
minutos | Puesta a punto ejes X y Z comprobaciones y control | 1 | 4,8 | 4,8 | 0,33 € | 1,58 €
minutos | Poner ajustar y quitar pinza con soporte cónico autocentrante | 3 | 0,7 | 2,1 | 0,33 € | 0,69 €
minutos | Montar, centrar/ ajustar y desmontar herramienta o portaherramienta de acabado | 1 | 0,85 | 0,85 | 0,33 € | 0,28 €
minutos | Montar herramienta en portaherramientas | 1 | 0,25 | 0,25 | 0,33 € | 0,08 €
minutos | Ajustar altura de la cuchilla | 1 | 0,42 | 0,42 | 0,33 € | 0,14 €
minutos | Comprobar alineación puntros eje y contracabezal con barra de prueba y comparador centesimal | 2 | 5 | 10 | 0,33 € | 3,31 €
minutos | Cambio de herramienta | 1 | 0,35 | 0,35 | 0,33 € | 0,12 €
minutos | Colocación del carro en posición de trabajo, ajustar pasada y aproximar herramienta a la pieza | 6 | 0,55 | 3,3 | 0,33 € | 1,09 €
minutos | Primera pasada de prueba, medir y volver a posición de trabajo | 2 | 0,15 | 0,3 | 0,33 € | 0,10 €
minutos | Sacar y volver a introducir la herramienta para eliminar viruta | 6 | 0,15 | 0,9 | 0,33 € | 0,30 €
minutos | Retirar carro, ajustar pasada con el nonio y volver a posición de trabajo | 6 | 0,55 | 3,3 | 0,33 € | 1,09 €
minutos | Comprobación de medidas | 2 | 0,3 | 0,6 | 0,33 € | 0,20 €
minutos | Comprobación medida final | 1 | 0,3 | 0,3 | 0,33 € | 0,10 €
minutos | Invertir pieza amarrada en plato universal | 2 | 0,3 | 0,6 | 0,33 € | 0,20 €
minutos | Colocación de fresa | 1 | 0,55 | 0,55 | 0,33 € | 0,18 €
minutos | Cilindrado de 1mm al árbol a ø35 h11. ø del cilíndro sin mecanizar ø45, largo del recorrido 267mm | 10 | 0,45 | 4,5 | 0,33 € | 1,49 €
minutos | Cilindrado de 1 mm, para llegar a dejarlo a 30mm longitud y ø28 | 30 | 0,45 | 13,5 | 0,33 € | 4,47 €
minutos | Refrentado de 1mm de caras hasta dejar el árbol a 267, siendo el cilindro a mecanizar de 280 | 13 | 0,5 | 6,5 | 0,33 € | 2,15 €

Capítulo | 01
Código | Ud

N

Tiempo total
de la
operación

Precio
unidad Importe

Reductora

Descripción

Cantidad (Kg o
min)
minutos | Fresado de 1 mm del chavetero 10x8x56 a la profundidad de fresado de 4,7 . | 4,7 | 0,38 | 1,786 | 0,33 € | 0,59 €
minutos | Fresado de 1mm del chavetero 10x8x56, a longitud 56 | 56 | 0,3 | 16,8 | 0,33 € | 5,56 €
minutos | Fresado de una acanaladura a 30 mm de longitud, 6 de ellas a ø28. | 6 | 4 | 24 | 0,33 € | 7,94 €
minutos | Achaflanado 1x45º en una cara, en total 2 caras | 2 | 0,8 | 1,6 | 0,33 € | 0,53 €
Tiempo total invertido en minutos | 129,64
Ud | horas
| 2,161
MO01 | horas | Oficial de 1ª Ferralista | 1 | 19,85 € | 42,89 €
Subtotal partida subcapítulo 01.2. (CD) | 67,68 €
| | | %Costes Indirectos (CI) | | 7%
| | | Total partida subcapítulo 01.2. | | 72,42 €
| | 01.2.1 Árbol de transmisión de salida

Ud

Kg | Cilindro Acero 37CrMo4 | 1 | 4,5 | | 6,70 € | 30,15 €
minutos | Estudiar plano y hoja de proceso | 1 | 2 | 2 | 0,33 € | 0,66 €
minutos | Recoger , limpiar y devolver piezas útiles de medición | 3 | 5,11 | 15,33 | 0,33 € | 5,06 €
minutos | Limpieza de la máquina | 1 | 15 | 15 | 0,33 € | 4,95 €
minutos | Puesta a punto ejes X y Z comprobaciones y control | 1 | 4,8 | 4,8 | 0,33 € | 1,58 €
minutos | Poner ajustar y quitar pinza con soporte cónico autocentrante | 3 | 0,7 | 2,1 | 0,33 € | 0,69 €
minutos | Montar, centrar/ ajustar y desmontar herramienta o portaherramienta de acabado | 1 | 0,85 | 0,85 | 0,33 € | 0,28 €
minutos | Montar herramienta en portaherramientas | 1 | 0,25 | 0,25 | 0,33 € | 0,08 €
minutos | Ajustar altura de la cuchilla | 1 | 0,42 | 0,42 | 0,33 € | 0,14 €
minutos | Comprobar alineación puntros eje y contracabezal con barra de prueba y comparador centesimal | 2 | 5 | 10 | 0,33 € | 3,31 €
minutos | Cambio de herramienta | 1 | 0,35 | 0,35 | 0,33 € | 0,12 €
minutos | Colocación del carro en posición de trabajo, ajustar pasada y aproximar herramienta a la pieza | 6 | 0,55 | 3,3 | 0,33 € | 1,09 €

Subcapítulo

Fabricación del árbol de transmisión de entrada de 267 mm de largo, Ø35 h11, fabricación asiento para la lengûeta plana de 10x8x56, achaflanado de extremos del árbol y fabricación en un extremo de nervado de longitud 30 y Ø32. Material empleado: Acero 37CrMo4

Capítulo | 01
Código | Ud

N

Tiempo total
de la
operación

Precio
unidad Importe

Reductora

Descripción

Cantidad (Kg o
min)
minutos | Primera pasada de prueba, medir y volver a posición de trabajo | 2 | 0,15 | 0,3 | 0,33 € | 0,10 €
minutos | Sacar y volver a introducir la herramienta para eliminar viruta | 6 | 0,15 | 0,9 | 0,33 € | 0,30 €
minutos | Retirar carro, ajustar pasada con el nonio y volver a posición de trabajo | 6 | 0,55 | 3,3 | 0,33 € | 1,09 €
minutos | Comprobación de medidas | 2 | 0,3 | 0,6 | 0,33 € | 0,20 €
minutos | Comprobación medida final | 1 | 0,3 | 0,3 | 0,33 € | 0,10 €
minutos | Invertir pieza amarrada en plato universal | 2 | 0,3 | 0,6 | 0,33 € | 0,20 €
minutos | Colocación de fresa | 1 | 0,55 | 0,55 | 0,33 € | 0,18 €
minutos | Cilindrado de 1mm al árbol a ø40 h11. ø del cilíndro sin mecanizar ø50 h11, largo de recorrido 267mm | 10 | 0,45 | 4,5 | 0,33 € | 1,49 €
minutos | Cilindrado de 1 mm, para llegar a dejarlo a 30mm longitud y ø36 | 30 | 0,45 | 13,5 | 0,33 € | 4,47 €
minutos | Refrentado de 1mm de caras hasta dejar el árbol a 267, siendo el cilindro a mecanizar de 280 | 13 | 0,5 | 6,5 | 0,33 € | 2,15 €
minutos | Fresado de 1 mm del chavetero 10x8x56 a la profundidad de fresado de 4,9 . | 4,9 | 0,38 | 1,862 | 0,33 € | 0,62 €
minutos | Fresado de 1mm del chavetero 12x8x56, a longitud 56 | 56 | 0,3 | 16,8 | 0,33 € | 5,56 €
minutos | Fresado de una acanaladura a 30 mm de longitud, 6 de ellas a ø36. | 6 | 4 | 24 | 0,33 € | 7,94 €
minutos | Achaflanado 1x45º en una cara, en total 2 caras | 2 | 0,8 | 1,6 | 0,33 € | 0,53 €
Tiempo total invertido en minutos | 129,71
Ud | horas
| 2,162
MO01 | horas | Oficial de 1ª Ferralista | 1 | 19,85 € | 42,91 €
Subtotal partida subcapítulo 01.2.1 (CD) | 73,06 €
| | | %Costes Indirectos (CI) | | 7%
| | | Total partida subcapítulo 01.2.1 | | 78,18 €
| | | Total partida subcapítulo 01.2 | | 150,59 €

### 01.3.0 Tapeta árbol de entrada

Ud

Tapetas

Subcapítulo

Fabricación de tapeta del árbol de entrada con su orificio pasante donde se inclurá el mecanizado del

Capítulo | 01
Código | Ud

N

Tiempo total
de la
operación

Precio
unidad Importe

Reductora

Descripción

Cantidad (Kg o
min)
Kg | Cilindro Acero C45 | 1 | 2 | | 6,00 € | 12,00 €
minutos | Estudiar plano y hoja de proceso | 1 | 2 | 2 | 0,33 € | 0,66 €
minutos | Recoger , limpiar y devolver piezas útiles | 3 | 5,11 | 15,33 | 0,33 € | 5,06 €
minutos | Limpieza de la máquina | 1 | 15 | 15 | 0,33 € | 4,95 €
minutos | Puesta a punto ejes X y Z comprobaciones y control | 1 | 4,8 | 4,8 | 0,33 € | 1,58 €
minutos | Poner ajustar y quitar pinza con soporte cónico autocentrante | 3 | 0,7 | 2,1 | 0,33 € | 0,69 €
minutos | Montar, centrar/ ajustar y desmontar herramienta o portaherramienta de acabado | 1 | 0,85 | 0,85 | 0,33 € | 0,28 €
minutos | Montar herramienta en portaherramientas | 1 | 0,25 | 0,25 | 0,33 € | 0,08 €
minutos | Ajustar altura de la cuchilla | 1 | 0,42 | 0,42 | 0,33 € | 0,14 €
minutos | Comprobar alineación puntros eje y contracabezal con barra de prueba y comparador centesimal | 2 | 5 | 10 | 0,33 € | 3,31 €
minutos | Cambio de herramienta | 1 | 0,35 | 0,35 | 0,33 € | 0,12 €
minutos | Colocación del carro en posición de trabajo, ajustar pasada y aproximar herramienta a la pieza | 6 | 0,55 | 3,3 | 0,33 € | 1,09 €
minutos | Primera pasada de prueba, medir y volver a posición de trabajo | 2 | 0,15 | 0,3 | 0,33 € | 0,10 €
minutos | Sacar y volver a introducir la herramienta para eliminar viruta | 6 | 0,15 | 0,9 | 0,33 € | 0,30 €
minutos | Retirar carro, ajustar pasada con el nonio y volver a posición de trabajo | 6 | 0,55 | 3,3 | 0,33 € | 1,09 €
minutos | Comprobación de medidas | 2 | 0,3 | 0,6 | 0,33 € | 0,20 €
minutos | Comprobación medida final | 1 | 0,3 | 0,3 | 0,33 € | 0,10 €
minutos | Invertir pieza amarrada en plato universal | 2 | 0,3 | 0,6 | 0,33 € | 0,20 €
minutos | Colocación de fresa | 1 | 0,55 | 0,55 | 0,33 € | 0,18 €
minutos | Cilindrado de 1mm al cilíndro a ø100, sin mecanizar ø110, largo de recorrido 25mm | 10 | 0,25 | 2,5 | 0,33 € | 0,83 €

Capítulo | 01
Código | Ud

N

Tiempo total
de la
operación

Precio
unidad Importe

Reductora

Descripción

Cantidad (Kg o
min)
minutos | Refrentado a 1mm, caras a 16mm, siendo el ancho del ciliindro sin mecanizar de 25 mm, en total 9 mm a mecanizar. Su ø100. | 9 | 1 | 9 | 0,33 € | 2,98 €
minutos | Cilindrado de 1mm en una cara para obtener ø62 j6 x 5 mm de longitud, por cada milímetro tarda 0,15 minutos, cilindra desde ø100. 38 mm en total | 38 | 0,15 | 5,7 | 0,33 € | 1,89 €
minutos | Cilindrado de 1mm en una cara para obtener ø62 x 3 mm de longitud, por cada milímetro tarda 0,07 minutos, cilindra desde ø100. 38 mm en total | 38 | 0,07 | 2,66 | 0,33 € | 0,88 €
minutos | Taladrado a ø5 para facilitar el taladrado de ø42, siendo ø5 por cada mm tarda 0,10 minutos | 16 | 0,08 | 1,28 | 0,33 € | 0,42 €
minutos | Taladrado a ø15 para facilitar el taladrado de ø42, siendo ø5 por cada mm tarda 0,13 minutos | 16 | 0,1 | 1,6 | 1,33 € | 2,13 €
minutos | Taladrado a ø25 para facilitar el taladrado de ø42, siendo ø5 por cada mm tarda 0,15 minutos | 16 | 0,13 | 2,08 | 2,33 € | 4,85 €
minutos | Fresado a ø42 concéntrico al cilíndro, el ancho es 16, por cada milímetro trada 0,19 minutos | 16 | 0,19 | 3,04 | 0,33 € | 1,01 €
minutos | Sin invertir la pieza a la cara que queda fresar a ø53x5mm de longitud, por cada milímetro tarda 0,5 minutos | 5 | 0,5 | 2,5 | 0,33 € | 0,83 €
minutos | Tras haber invertido la pieza fresar a ø45 | 7 | 0,45 | 3,15 | 0,33 € | 1,04 €
minutos | Taladrado de ø8,5 x 9 mm de longitud, por | 4 | 0,9 | 3,6 | 0,33 € | 1,19 €
Tiempo total invertido en minutos | 98,06
Ud | horas
| 1,634
MO01 | horas | Oficial de 1ª Ferralista | 1 | 19,85 € | 32,44 €
| | | Subtotal partida subcapítulo 01.3 (CD) | | 44,44 €
| | | %Costes Indirectos (CI) | | 7%
| | | Total partida subcapítulo 01.3 | | 47,55 €
| | 01.3.1 Tapeta ciega árbol de entrada
| Ud
Kg | Cilindro Acero C45 | 1 | 2 | | 6,00 € | 12,00 €
minutos | Estudiar plano y hoja de proceso | 1 | 2 | 2 | 0,33 € | 0,66 €

Subcapítulo

Fabricación de tapeta del árbol de entrada agujero ciego , mecanizado a ø100x16 de ancho, de incluirá el

Capítulo | 01
Código | Ud

N

Tiempo total
de la
operación

Precio
unidad Importe

Reductora

Descripción

Cantidad (Kg o
min)
minutos | Recoger , limpiar y devolver piezas útiles | 3 | 5,11 | 15,33 | 0,33 € | 5,06 €
minutos | Limpieza de la máquina | 1 | 15 | 15 | 0,33 € | 4,95 €
minutos | Puesta a punto ejes X y Z comprobaciones y control | 1 | 4,8 | 4,8 | 0,33 € | 1,58 €
minutos | Poner ajustar y quitar pinza con soporte cónico autocentrante | 3 | 0,7 | 2,1 | 0,33 € | 0,69 €
minutos | Montar, centrar/ ajustar y desmontar herramienta o portaherramienta de acabado | 1 | 0,85 | 0,85 | 0,33 € | 0,28 €
minutos | Montar herramienta en portaherramientas | 1 | 0,25 | 0,25 | 0,33 € | 0,08 €
minutos | Ajustar altura de la cuchilla | 1 | 0,42 | 0,42 | 0,33 € | 0,14 €
minutos | Comprobar alineación puntros eje y contracabezal con barra de prueba y comparador centesimal | 2 | 5 | 10 | 0,33 € | 3,31 €
minutos | Cambio de herramienta | 1 | 0,35 | 0,35 | 0,33 € | 0,12 €
minutos | Colocación del carro en posición de trabajo, ajustar pasada y aproximar herramienta a la pieza | 6 | 0,55 | 3,3 | 0,33 € | 1,09 €
minutos | Primera pasada de prueba, medir y volver a posición de trabajo | 2 | 0,15 | 0,3 | 0,33 € | 0,10 €
minutos | Sacar y volver a introducir la herramienta para eliminar viruta | 6 | 0,15 | 0,9 | 0,33 € | 0,30 €
minutos | Retirar carro, ajustar pasada con el nonio y volver a posición de trabajo | 6 | 0,55 | 3,3 | 0,33 € | 1,09 €
minutos | Comprobación de medidas | 2 | 0,3 | 0,6 | 0,33 € | 0,20 €
minutos | Comprobación medida final | 1 | 0,3 | 0,3 | 0,33 € | 0,10 €
minutos | Invertir pieza amarrada en plato universal | 2 | 0,3 | 0,6 | 0,33 € | 0,20 €
minutos | Colocación de fresa | 1 | 0,55 | 0,55 | 0,33 € | 0,18 €
minutos | Cilindrado de 1mm al cilíndro a ø100, sin mecanizar ø110, largo de recorrido 25mm | 10 | 0,25 | 2,5 | 0,33 € | 0,83 €
minutos | Refrentado a 1mm, caras a 13mm, siendo el ancho del ciliindro sin mecanizar de 25 mm, en total 12 mm a mecanizar. Su ø100. | 12 | 1 | 12 | 0,33 € | 3,97 €
minutos | Cilindrado de 1mm en una cara para obtener ø62 j6 x 5 mm de longitud, por cada milímetro tarda 0,15 minutos, cilindra desde ø100. 38 mm en total | 38 | 0,15 | 5,7 | 0,33 € | 1,89 €
minutos | Taladrado a ø5 para facilitar el taladrado de ø42, siendo ø5 por cada mm tarda 0,10 minutos | 16 | 0,08 | 1,28 | 0,33 € | 0,42 €

Capítulo | 01
Código | Ud

N

Tiempo total
de la
operación

Precio
unidad Importe

Reductora

Descripción

Cantidad (Kg o
min)
minutos | 4 | 3,6 | 0,33 € | 1,19 €
Tiempo total invertido en minutos | 86,03
Ud | horas
| 1,434
MO01 | horas | Oficial de 1ª Ferralista | 1 | 19,85 € | 28,46 €
Subtotal partida subcapítulo 01.3.1 (CD) | 40,46 €
| | | %Costes Indirectos (CI) | | 7%
| | | Total partida subcapítulo 01.3.1 | | 43,29 €
| | 01.3.2 Tapeta árbol de salida

Ud

Kg | Cilindro Acero C45 | 1 | 2 | | 6,00 € | 12,00 €
minutos | Estudiar plano y hoja de proceso | 1 | 2 | 2 | 0,33 € | 0,66 €
minutos | Recoger , limpiar y devolver piezas útiles de medición | 3 | 5,11 | 15,33 | 0,33 € | 5,06 €
minutos | Limpieza de la máquina | 1 | 15 | 15 | 0,33 € | 4,95 €
minutos | Puesta a punto ejes X y Z comprobaciones y control | 1 | 4,8 | 4,8 | 0,33 € | 1,58 €
minutos | Poner ajustar y quitar pinza con soporte cónico autocentrante | 3 | 0,7 | 2,1 | 0,33 € | 0,69 €
minutos | Montar, centrar/ ajustar y desmontar herramienta o portaherramienta de acabado | 1 | 0,85 | 0,85 | 0,33 € | 0,28 €
minutos | Montar herramienta en portaherramientas | 1 | 0,25 | 0,25 | 0,33 € | 0,08 €
minutos | Ajustar altura de la cuchilla | 1 | 0,42 | 0,42 | 0,33 € | 0,14 €
minutos | Comprobar alineación puntros eje y contracabezal con barra de prueba y comparador centesimal | 2 | 5 | 10 | 0,33 € | 3,31 €
minutos | Cambio de herramienta | 1 | 0,35 | 0,35 | 0,33 € | 0,12 €
minutos | Colocación del carro en posición de trabajo, ajustar pasada y aproximar herramienta a la pieza | 6 | 0,55 | 3,3 | 0,33 € | 1,09 €
minutos | Primera pasada de prueba, medir y volver a posición de trabajo | 2 | 0,15 | 0,3 | 0,33 € | 0,10 €

Subcapítulo

Fabricación de tapeta del árbol de entrada con su orificio pasante donde se inclurá el mecanizado del habitáculo del retén, mecanizado a ø100x16 de ancho, de incluirá el taladrado de 4 orificios pasantes de ø8,5, el habitáculo donde se acopla el retén tendrá una tolerancia de 45 H8. Material empleado: C45

Taladrado de ø8,5 x 9 mm de longitud, por
cada taladrado tarda 0,9 minutos | 0,9

Capítulo | 01
Código | Ud

N

Tiempo total
de la
operación

Precio
unidad Importe

Reductora

Descripción

Cantidad (Kg o
min)
minutos | Sacar y volver a introducir la herramienta para eliminar viruta | 6 | 0,15 | 0,9 | 0,33 € | 0,30 €
minutos | Retirar carro, ajustar pasada con el nonio y volver a posición de trabajo | 6 | 0,55 | 3,3 | 0,33 € | 1,09 €
minutos | Comprobación de medidas | 2 | 0,3 | 0,6 | 0,33 € | 0,20 €
minutos | Comprobación medida final | 1 | 0,3 | 0,3 | 0,33 € | 0,10 €
minutos | Invertir pieza amarrada en plato universal | 2 | 0,3 | 0,6 | 0,33 € | 0,20 €
minutos | Colocación de fresa | 1 | 0,55 | 0,55 | 0,33 € | 0,18 €
minutos | Cilindrado de 1mm al cilíndro a ø100, sin mecanizar ø110, largo de recorrido 25mm | 10 | 0,25 | 2,5 | 0,33 € | 0,83 €
minutos | Refrentado a 1mm, caras a 16mm, siendo el ancho del ciliindro sin mecanizar de 25 mm, en total 9 mm a mecanizar. Su ø100. | 9 | 1 | 9 | 0,33 € | 2,98 €
minutos | Cilindrado de 1mm en una cara para obtener ø68 j6 x 5 mm de longitud, por cada milímetro tarda 0,15 minutos, cilindra desde ø100. 32 mm en total | 32 | 0,15 | 4,8 | 0,33 € | 1,59 €
minutos | Cilindrado de 1mm en una cara para obtener ø68 x 3 mm de longitud, por cada milímetro tarda 0,07 minutos, cilindra desde ø100. 32 mm en total | 32 | 0,07 | 2,24 | 0,33 € | 0,74 €
minutos | Taladrado a ø5 para facilitar el taladrado de ø47, siendo ø5 por cada mm tarda 0,10 minutos (16 mm de longitud) | 16 | 0,08 | 1,28 | 0,33 € | 0,42 €
minutos | Taladrado a ø15 para facilitar el taladrado de ø47, siendo ø15 por cada mm tarda 0,13 minutos | 16 | 0,1 | 1,6 | 1,33 € | 2,13 €
minutos | Taladrado a ø25 para facilitar el taladrado de ø47, siendo ø25 por cada mm tarda 0,17 minutos | 16 | 0,17 | 2,72 | 2,33 € | 6,34 €
minutos | Fresado a ø47 concéntrico al cilíndro, el ancho es 16, por cada milímetro trada 0,22 minutos | 16 | 0,22 | 3,52 | 0,33 € | 1,16 €
minutos | Sin invertir la pieza a la cara que queda fresar a ø58x5mm de longitud, por cada milímetro tarda 0,55 minutos | 5 | 0,55 | 2,75 | 0,33 € | 0,91 €
minutos | Tras haber invertido la pieza fresar a ø52 H8x7mm de longitud, por cada milímetro tarda 0,5 minutos | 7 | 0,5 | 3,5 | 0,33 € | 1,16 €
minutos | Taladrado de ø8,5 x 9 mm de longitud, por cada taladrado tarda 0,9 minutos | 4 | 0,9 | 3,6 | 0,33 € | 1,19 €

Capítulo | 01
Código | Ud

N

Tiempo total
de la
operación

Precio
unidad Importe

Reductora

Descripción

Cantidad (Kg o
min)
Tiempo total invertido en minutos | 98,46
Ud | horas
| 1,641
MO01 | horas | Oficial de 1ª Ferralista | 1 | 19,85 € | 32,57 €
Subtotal partida subcapítulo 01.3.2 (CD) | 44,57 €
| | | %Costes Indirectos (CI) | | 7%
| | | Total partida subcapítulo 01.3.2 | | 47,69 €
| | 01.3.3 Tapeta ciega árbol de salida
| Ud
Kg | Cilindro Acero C45 | 1 | 2 | | 6,00 € | 12,00 €
minutos | Estudiar plano y hoja de proceso | 1 | 2 | 2 | 0,33 € | 0,66 €
minutos | Recoger , limpiar y devolver piezas útiles de medición | 3 | 5,11 | 15,33 | 0,33 € | 5,06 €
minutos | Limpieza de la máquina | 1 | 15 | 15 | 0,33 € | 4,95 €
minutos | Puesta a punto ejes X y Z comprobaciones y control | 1 | 4,8 | 4,8 | 0,33 € | 1,58 €
minutos | Poner ajustar y quitar pinza con soporte cónico autocentrante | 3 | 0,7 | 2,1 | 0,33 € | 0,69 €
minutos | Montar, centrar/ ajustar y desmontar herramienta o portaherramienta de acabado | 1 | 0,85 | 0,85 | 0,33 € | 0,28 €
minutos | Montar herramienta en portaherramientas | 1 | 0,25 | 0,25 | 0,33 € | 0,08 €
minutos | Ajustar altura de la cuchilla | 1 | 0,42 | 0,42 | 0,33 € | 0,14 €
minutos | Comprobar alineación puntros eje y contracabezal con barra de prueba y comparador centesimal | 2 | 5 | 10 | 0,33 € | 3,31 €
minutos | Cambio de herramienta | 1 | 0,35 | 0,35 | 0,33 € | 0,12 €
minutos | Colocación del carro en posición de trabajo, ajustar pasada y aproximar herramienta a la pieza | 6 | 0,55 | 3,3 | 0,33 € | 1,09 €
minutos | Primera pasada de prueba, medir y volver a posición de trabajo | 2 | 0,15 | 0,3 | 0,33 € | 0,10 €
minutos | Sacar y volver a introducir la herramienta para eliminar viruta | 6 | 0,15 | 0,9 | 0,33 € | 0,30 €
minutos | Retirar carro, ajustar pasada con el nonio y volver a posición de trabajo | 6 | 0,55 | 3,3 | 0,33 € | 1,09 €
minutos | Comprobación de medidas | 2 | 0,3 | 0,6 | 0,33 € | 0,20 €
minutos | | 1 | 0,3 | 0,3 | 0,33 € | 0,10 € Comprobación medida final

Subcapítulo

Fabricación de tapeta del árbol de entrada agujero ciego , mecanizado a ø100x16 de ancho, de incluirá el taladrado de 4 orificios pasantes de ø8,5. Material empleado: C45

Capítulo | 01
Código | Ud

N

Tiempo total
de la
operación

Precio
unidad Importe

Reductora

Descripción

Cantidad (Kg o
min)
minutos | Invertir pieza amarrada en plato universal | 2 | 0,3 | 0,6 | 0,33 € | 0,20 €
minutos | Colocación de fresa | 1 | 0,55 | 0,55 | 0,33 € | 0,18 €
minutos | Cilindrado de 1mm al cilíndro a ø100, sin mecanizar ø110, largo de recorrido 25mm | 10 | 0,25 | 2,5 | 0,33 € | 0,83 €
minutos | Refrentado a 1mm, caras a 13mm, siendo el ancho del ciliindro sin mecanizar de 25 mm, en total 12 mm a mecanizar. Su ø100. | 12 | 1 | 12 | 0,33 € | 3,97 €
minutos | Cilindrado de 1mm en una cara para obtener ø68 j6 x 5 mm de longitud, por cada milímetro tarda 0,15 minutos, cilindra desde ø100. 32 mm en total | 32 | 0,15 | 4,8 | 0,33 € | 1,59 €
minutos | Taladrado a ø5 para facilitar el taladrado de ø42, siendo ø5 por cada mm tarda 0,10 minutos | 16 | 0,08 | 1,28 | 0,33 € | 0,42 €
minutos | Taladrado de ø8,5 x 9 mm de longitud, por cada taladrado tarda 0,9 minutos | 4 | 0,9 | 3,6 | 0,33 € | 1,19 €
Tiempo total invertido en minutos | 85,13
Ud | horas
| 1,419
MO01 | horas | Oficial de 1ª Ferralista | 1 | 19,85 € | 28,16 €
Subtotal partida subcapítulo 01.3.3 (CD) | 40,16 €
| | | %Costes Indirectos (CI) | | 7%
| | | Total partida subcapítulo 01.3.3 | | 42,98 €
| | | Total partida subcapítulo 01.3 | | 181,52 €

### 01.4.0 Casquillo separador árbol de entrada

Ud

Kg | Cilindro Bronce 1998 CC493K | 1 | 1,5 | | 5,76 € | 8,64 €
minutos | Estudiar plano y hoja de proceso | 1 | 2 | 2 | 0,33 € | 0,66 €
minutos | Recoger , limpiar y devolver piezas útiles de medición | 3 | 5,11 | 15,33 | 0,33 € | 5,06 €
minutos | Limpieza de la máquina | 1 | 15 | 15 | 0,33 € | 4,95 €
minutos | Puesta a punto ejes X y Z comprobaciones y control | 1 | 4,8 | 4,8 | 0,33 € | 1,58 €
minutos | Poner ajustar y quitar pinza con soporte cónico autocentrante | 3 | 0,7 | 2,1 | 0,33 € | 0,69 €

Subcapítulo

Fabricación de una unidad de casquillo separador árbol de entrada, en el prosupuesto se contarán 2

Casquillos

Capítulo | 01
Código | Ud

N

Tiempo total
de la
operación

Precio
unidad Importe

Reductora

Descripción

Cantidad (Kg o
min)
minutos | Montar, centrar/ ajustar y desmontar herramienta o portaherramienta de acabado | 1 | 0,85 | 0,85 | 0,33 € | 0,28 €
minutos | Montar herramienta en portaherramientas | 1 | 0,25 | 0,25 | 0,33 € | 0,08 €
minutos | Ajustar altura de la cuchilla | 1 | 0,42 | 0,42 | 0,33 € | 0,14 €
minutos | Comprobar alineación puntros eje y contracabezal con barra de prueba y comparador centesimal | 2 | 5 | 10 | 0,33 € | 3,31 €
minutos | Cambio de herramienta | 1 | 0,35 | 0,35 | 0,33 € | 0,12 €
minutos | Colocación del carro en posición de trabajo, ajustar pasada y aproximar herramienta a la pieza | 6 | 0,55 | 3,3 | 0,33 € | 1,09 €
minutos | Primera pasada de prueba, medir y volver a posición de trabajo | 2 | 0,15 | 0,3 | 0,33 € | 0,10 €
minutos | Sacar y volver a introducir la herramienta para eliminar viruta | 6 | 0,15 | 0,9 | 0,33 € | 0,30 €
minutos | Retirar carro, ajustar pasada con el nonio y volver a posición de trabajo | 6 | 0,55 | 3,3 | 0,33 € | 1,09 €
minutos | Comprobación de medidas | 2 | 0,3 | 0,6 | 0,33 € | 0,20 €
minutos | Comprobación medida final | 1 | 0,3 | 0,3 | 0,33 € | 0,10 €
minutos | Invertir pieza amarrada en plato universal | 2 | 0,3 | 0,6 | 0,33 € | 0,20 €
minutos | Colocación de fresa | 1 | 0,55 | 0,55 | 0,33 € | 0,18 €
minutos | Cilindrado de 1mm al cilíndro a 45, sin mecanizar ø55, largo de recorrido 25mm | 10 | 0,25 | 2,5 | 0,33 € | 0,83 €
minutos | Refrentado a 1mm, caras a 15mm, siendo el ancho del cilindro sin mecanizar de 25 mm, en total 10 mm a mecanizar. Su ø100. | 10 | 1 | 10 | 0,33 € | 3,31 €
minutos | Taladrado a ø5 para facilitar el taladrado de ø35 H7, siendo ø5 por cada mm tarda 0,10 minutos (16 mm de longitud) | 16 | 0,08 | 1,28 | 0,33 € | 0,42 €
minutos | Taladrado a ø15 para facilitar el fresado de ø35 H7 , siendo ø15 por cada mm tarda 0,13 minutos | 16 | 0,1 | 1,6 | 1,33 € | 2,13 €
minutos | Taladrado a ø25 para facilitar el taladrado de ø35 H7, siendo ø25 por cada mm tarda 0,17 minutos | 16 | 0,17 | 2,72 | 2,33 € | 6,34 €
minutos | Fresado a ø35 H7 concéntrico al cilíndro, el ancho es 15, por cada milímetro trada 0,15 minutos | 16 | 0,15 | 2,4 | 0,33 € | 0,79 €
Tiempo total invertido en minutos | 81,45

Capítulo | 01
Código | Ud

N

Tiempo total
de la
operación

Precio
unidad Importe

Reductora

Descripción

Cantidad (Kg o
min)
Ud | horas
| 1,358
MO01 | horas | Oficial de 1ª Ferralista | 1 | 19,85 € | 26,95 €
| | | Subtotal partida subcapítulo 01.4 (CD) | | 35,59 €
| | | %Costes Indirectos (CI) | | 7%
| | | Total partida subcapítulo 01.4 | | 38,08 €
| | 01.4.1 Casquillo separador árbol de salida
| Ud
Kg | Cilindro Bronce 1998 CC493K | 1 | 1,5 | | 5,76 € | 8,64 €
minutos | Estudiar plano y hoja de proceso | 1 | 2 | 2 | 0,33 € | 0,66 €
minutos | Recoger , limpiar y devolver piezas útiles | 3 | 5,11 | 15,33 | 0,33 € | 5,06 €
minutos | Limpieza de la máquina | 1 | 15 | 15 | 0,33 € | 4,95 €
minutos | Puesta a punto ejes X y Z comprobaciones y control | 1 | 4,8 | 4,8 | 0,33 € | 1,58 €
minutos | Poner ajustar y quitar pinza con soporte cónico autocentrante | 3 | 0,7 | 2,1 | 0,33 € | 0,69 €
minutos | Montar, centrar/ ajustar y desmontar herramienta o portaherramienta de acabado | 1 | 0,85 | 0,85 | 0,33 € | 0,28 €
minutos | Montar herramienta en portaherramientas | 1 | 0,25 | 0,25 | 0,33 € | 0,08 €
minutos | Ajustar altura de la cuchilla | 1 | 0,42 | 0,42 | 0,33 € | 0,14 €
minutos | Comprobar alineación puntros eje y contracabezal con barra de prueba y comparador centesimal | 2 | 5 | 10 | 0,33 € | 3,31 €
minutos | Cambio de herramienta | 1 | 0,35 | 0,35 | 0,33 € | 0,12 €
minutos | Colocación del carro en posición de trabajo, ajustar pasada y aproximar herramienta a la pieza | 6 | 0,55 | 3,3 | 0,33 € | 1,09 €
minutos | Primera pasada de prueba, medir y volver a posición de trabajo | 2 | 0,15 | 0,3 | 0,33 € | 0,10 €
minutos | Sacar y volver a introducir la herramienta para eliminar viruta | 6 | 0,15 | 0,9 | 0,33 € | 0,30 €
minutos | Retirar carro, ajustar pasada con el nonio y volver a posición de trabajo | 6 | 0,55 | 3,3 | 0,33 € | 1,09 €
minutos | Comprobación de medidas | 2 | 0,3 | 0,6 | 0,33 € | 0,20 €
minutos | Comprobación medida final | 1 | 0,3 | 0,3 | 0,33 € | 0,10 €
minutos | Invertir pieza amarrada en plato universal | 2 | 0,3 | 0,6 | 0,33 € | 0,20 €
minutos | Colocación de fresa | 1 | 0,55 | 0,55 | 0,33 € | 0,18 €
minutos | Cilindrado de 1mm al cilíndro a ø50, sin mecanizar ø60, largo de recorrido 25mm | 10 | 0,25 | 2,5 | 0,33 € | 0,83 €

Subcapítulo

Fabricación de una unidad de casquillo separador árbol de entrada, en el prosupuesto se contarán 2

Capítulo | 01
Código | Ud

N

Tiempo total
de la
operación

Precio
unidad Importe

Reductora

Descripción

Cantidad (Kg o
min)
minutos | Refrentado a 1mm, caras a 15mm, siendo el ancho del cilindro sin mecanizar de 25 mm, en total 10 mm a mecanizar. Su ø100. | 10 | 1 | 10 | 0,33 € | 3,31 €
minutos | Taladrado a ø5 para facilitar el taladrado de ø40 H7, siendo ø5 por cada mm tarda 0,10 minutos (16 mm de longitud) | 16 | 0,08 | 1,28 | 0,33 € | 0,42 €
minutos | Taladrado a ø15 para facilitar el fresado de ø40 H7 , siendo ø15 por cada mm tarda 0,13 minutos | 16 | 0,1 | 1,6 | 1,33 € | 2,13 €
minutos | Taladrado a ø25 para facilitar el taladrado de ø40 H7, siendo ø25 por cada mm tarda 0,17 minutos | 16 | 0,17 | 2,72 | 2,33 € | 6,34 €
minutos | Fresado a ø40 H7 concéntrico al cilíndro, el ancho es 15, por cada milímetro trada 0,35 minutos | 16 | 0,35 | 5,6 | 0,33 € | 1,85 €
Tiempo total invertido en minutos | 84,65
Ud | horas
| 1,411
MO01 | horas | Oficial de 1ª Ferralista | 1 | 19,85 € | 28,01 €
Subtotal partida subcapítulo 01.4.1 (CD) | 36,65 €
| | | %Costes Indirectos (CI) | | 7%
| | | Total partida subcapítulo 01.4.1 | | 39,21 €
| | | | | 77,29 €

### 01.5.0 Caja de la reductora parte inferior

Ud

Kg | Cilindro Acero C45 | 1 | 39 | | 6,00 € | 234,00 €
minutos | Estudiar plano y hoja de proceso | 1 | 2 | 2 | 0,33 € | 0,66 €
minutos | Recoger , limpiar y devolver piezas útiles de medición | 3 | 5,11 | 15,33 | 0,33 € | 5,06 €
minutos | Limpieza de la máquina | 1 | 15 | 15 | 0,33 € | 4,95 €
minutos | Puesta a punto ejes X y Z comprobaciones y control | 1 | 4,8 | 4,8 | 0,33 € | 1,58 €
minutos | Poner ajustar y quitar pinza con soporte cónico autocentrante | 3 | 0,7 | 2,1 | 0,33 € | 0,69 €

Caja

Subcapítulo

Fabricación de la caja parte inferior en la que incluye su propia base, la forma de esta caja se realizará por

Total partida subcapítulo 01.4 solo contando un casquillo por
subcapítulo

Capítulo | 01
Código | Ud

N

Tiempo total
de la
operación

Precio
unidad Importe

Reductora

Descripción

Cantidad (Kg o
min)
minutos | Montar, centrar/ ajustar y desmontar herramienta o portaherramienta de acabado | 1 | 0,85 | 0,85 | 0,33 € | 0,28 €
minutos | Montar herramienta en portaherramientas | 1 | 0,25 | 0,25 | 0,33 € | 0,08 €
minutos | Ajustar altura de la cuchilla | 1 | 0,42 | 0,42 | 0,33 € | 0,14 €
minutos | Comprobar alineación puntros eje y contracabezal con barra de prueba y comparador centesimal | 2 | 5 | 10 | 0,33 € | 3,31 €
minutos | Cambio de herramienta | 1 | 0,35 | 0,35 | 0,33 € | 0,12 €
minutos | Colocación del carro en posición de trabajo, ajustar pasada y aproximar herramienta a la pieza | 6 | 0,55 | 3,3 | 0,33 € | 1,09 €
minutos | Primera pasada de prueba, medir y volver a posición de trabajo | 2 | 0,15 | 0,3 | 0,33 € | 0,10 €
minutos | Sacar y volver a introducir la herramienta para eliminar viruta | 6 | 0,15 | 0,9 | 0,33 € | 0,30 €
minutos | Retirar carro, ajustar pasada con el nonio y volver a posición de trabajo | 6 | 0,55 | 3,3 | 0,33 € | 1,09 €
minutos | Comprobación de medidas | 2 | 0,3 | 0,6 | 0,33 € | 0,20 €
minutos | Comprobación medida final | 1 | 0,3 | 0,3 | 0,33 € | 0,10 €
minutos | Invertir pieza amarrada en plato universal | 2 | 0,3 | 0,6 | 0,33 € | 0,20 €
minutos | Colocación de fresa | 1 | 0,55 | 0,55 | 0,33 € | 0,18 €
minutos | Corte de pletinas laterales | 2 | 1,2 | 2,4 | 0,33 € | 0,79 €
minutos | Corte de pletinas posterior y delantera | 1 | 2 | 2 | 0,33 € | 0,66 €
minutos | Corte de pletina base | 1 | 2,3 | 2,3 | 0,33 € | 0,76 €
minutos | Corte de pletinas de reborde | 2 | 1 | 2 | 0,33 € | 0,66 €
minutos | Limpieza de rebabas | 1 | 4 | 4 | 0,33 € | 1,32 €
minutos | Trazado de circunferencias pletinas laterales 34 H7 y 32 H7 | 1 | 3,5 | 3,5 | 0,33 € | 1,16 €
minutos | Trazado de taladros pletinas laterales M8 | 1 | 1,2 | 1,2 | 0,33 € | 0,40 €
minutos | Trazado de taladros pletina base M12 | 1 | 1,25 | 1,25 | 0,33 € | 0,41 €
minutos | Trazado de taladros pletinas de reborde M6 | 1 | 5 | 5 | 0,33 € | 1,65 €
minutos | Taladrado a ø5 para facilitar el taladrado de ø34 H7, siendo ø5 por cada mm tarda 0,10 minutos (25 mm de espesor) | 25 | 0,08 | 2 | 0,33 € | 0,66 €

Capítulo | 01
Código | Ud

N

Tiempo total
de la
operación

Precio
unidad Importe

Reductora

Descripción

Cantidad (Kg o
min)
minutos | Taladrado a ø15 para facilitar el fresado de ø34 H7 , siendo ø10 por cada mm tarda 0,13 minutos | 25 | 0,1 | 2,5 | 1,33 € | 3,33 €
minutos | Taladrado a ø25 para facilitar el taladrado de ø34 H7, siendo ø25 por cada mm tarda 0,17 minutos | 25 | 0,17 | 4,25 | 2,33 € | 9,91 €
minutos | Fresado y planear hasta dejar la pletina en espesor 14, donde se respetarán los rebordes semicirculares de diámetro 100 que conservará el mismo espesor que tenia la pletina orginal. 11mm se deben retirar, por cada mm de profundidad a lo largo de la pletina (358mmx85,5) tarda 2 minutos | 11 | 2 | 22 | 2,33 € | 51,28 €
minutos | Taladrado a ø5 para facilitar el taladrado de ø34 H7, siendo ø5 por cada mm tarda 0,10 minutos (25 mm de espesor) (la pletina opuesta) | 25 | 0,08 | 2 | 0,33 € | 0,66 €
minutos | Taladrado a ø15 para facilitar el fresado de ø34 H7 , siendo ø10 por cada mm tarda 0,13 minutos | 25 | 0,1 | 2,5 | 1,33 € | 3,33 €
minutos | Taladrado a ø25 para facilitar el taladrado de ø34 H7, siendo ø25 por cada mm tarda 0,17 minutos | 25 | 0,17 | 4,25 | 2,33 € | 9,91 €
minutos | Fresado y planear hasta dejar la pletina en espesor 14, donde se respetarán los rebordes semicirculares de diámetro 100 que conservará el mismo espesor que | 11 | 2 | 22 | 2,33 € | 51,28 €
minutos | Taladrado a ø5 para facilitar el taladrado de M12, siendo ø5 por cada mm tarda 0,10 minutos (25 mm de espesor) | 15 | 0,08 | 1,2 | 0,33 € | 0,40 €
minutos | Taladrado de pletinas de base, cada taladro tarda 0,36 minutos | 4 | 0,36 | 1,44 | 2,33 € | 3,36 €
minutos | Realizar roscado con macho de roscar a M12 | 4 | 2,8 | 11,2 | 2,33 € | 26,11 €
minutos | Taladrado de tapón de vaciado M16 pletina base, 0,4 minutos el taladro | 1 | 0,4 | 0,4 | 2,33 € | 0,93 €
minutos | Realizar roscado con macho de roscar a M16 | 1 | 3 | 3 | 2,33 € | 6,99 €

Capítulo | 01
Código | Ud

N

Tiempo total
de la
operación

Precio
unidad Importe

Reductora

Descripción

Cantidad (Kg o
min)
minutos | Taladrado de pletinas de reborde, cada taladro tarda 0,36 minutos | 14 | 0,36 | 5,04 | 2,33 € | 11,75 €
minutos | Realizar roscado con macho de roscar a M6 | 14 | 0,2 | 2,8 | 2,33 € | 6,53 €
minutos | Taladrado M8 para la fijación de las tapetas, 2 taladros por cada circunferencia. La longitud del taladrado es finita a 10mm | 4 | 0,09 | 0,36 | 2,33 € | 0,84 €
minutos | Realizar roscado con macho de roscar a M8 | 4 | 1,5 | 6 | 2,33 € | 13,98 €
minutos | Taladrado M8 para la fijación de las tapetas, (pletina opuesta) 2 taladros por cada circunferencia. La longitud del taladrado es finita a 10mm | 4 | 0,09 | 0,36 | 2,33 € | 0,84 €
minutos | Realizar roscado con macho de roscar a M8 | 4 | 1,5 | 6 | 2,33 € | 13,98 €
minutos | Proceso de soldadura en ángulo para las pletinas laterales, 1,3 minutos por unidad | 2 | 1,8 | 3,6 | 2,33 € | 8,39 €
minutos | Proceso de soldadura en ángulo en las paredes posterior y delantera, 0,45 minutos por unidad | 2 | 0,45 | 0,9 | 2,33 € | 2,10 €
minutos | Proceso de soldadura en ángulo para las pletinas de reborde 2,5 minutos el reborde entero. | 1 | 2,5 | 2,5 | 2,33 € | 5,83 €
minutos | Limpieza de escoria y cepillado | 1 | 2,5 | 2,5 | 2,33 € | 5,83 €
minutos | Comprobación de soldadura | 1 | 4 | 4 | 2,33 € | 9,32 €
minutos | Uso del grupo de soldadura | 1 | 7 | 7 | 2,33 € | 16,32 €
Tiempo total invertido en minutos | 204,40
Ud | horas
| 3,407
MO01 | horas | Oficial de 1ª Ferralista | 1 | 19,85 € | 67,62 €
| | | Subtotal partida subcapítulo 01.5 (CD) | | 301,62 €
| | | %Costes Indirectos (CI) | | 7%
| | | Total partida subcapítulo 01.5 | | 322,74 €
| | 01.5.1 Caja de la reductora parte superior

Subcapítulo

Capítulo | 01
Código | Ud

N

Tiempo total
de la
operación

Precio
unidad Importe

Reductora

Descripción

Cantidad (Kg o
min)

Ud

Kg | Cilindro Acero C45 | 1 | 35,5 | | 6,00 € | 213,00 €
minutos | Estudiar plano y hoja de proceso | 1 | 2 | 2 | 0,33 € | 0,66 €
minutos | Recoger , limpiar y devolver piezas útiles de medición | 3 | 5,11 | 15,33 | 0,33 € | 5,06 €
minutos | Limpieza de la máquina | 1 | 15 | 15 | 0,33 € | 4,95 €
minutos | Puesta a punto ejes X y Z comprobaciones y control | 1 | 4,8 | 4,8 | 0,33 € | 1,58 €
minutos | Poner ajustar y quitar pinza con soporte cónico autocentrante | 3 | 0,7 | 2,1 | 0,33 € | 0,69 €
minutos | Montar, centrar/ ajustar y desmontar herramienta o portaherramienta de acabado | 1 | 0,85 | 0,85 | 0,33 € | 0,28 €
minutos | Montar herramienta en portaherramientas | 1 | 0,25 | 0,25 | 0,33 € | 0,08 €
minutos | Ajustar altura de la cuchilla | 1 | 0,42 | 0,42 | 0,33 € | 0,14 €
minutos | Comprobar alineación puntros eje y contracabezal con barra de prueba y comparador centesimal | 2 | 5 | 10 | 0,33 € | 3,31 €
minutos | Cambio de herramienta | 1 | 0,35 | 0,35 | 0,33 € | 0,12 €
minutos | Colocación del carro en posición de trabajo, ajustar pasada y aproximar herramienta a la pieza | 6 | 0,55 | 3,3 | 0,33 € | 1,09 €
minutos | Primera pasada de prueba, medir y volver a posición de trabajo | 2 | 0,15 | 0,3 | 0,33 € | 0,10 €
minutos | Sacar y volver a introducir la herramienta para eliminar viruta | 6 | 0,15 | 0,9 | 0,33 € | 0,30 €
minutos | Retirar carro, ajustar pasada con el nonio y volver a posición de trabajo | 6 | 0,55 | 3,3 | 0,33 € | 1,09 €
minutos | Comprobación de medidas | 2 | 0,3 | 0,6 | 0,33 € | 0,20 €
minutos | Comprobación medida final | 1 | 0,3 | 0,3 | 0,33 € | 0,10 €
minutos | Invertir pieza amarrada en plato universal | 2 | 0,3 | 0,6 | 0,33 € | 0,20 €
minutos | Colocación de fresa | 1 | 0,55 | 0,55 | 0,33 € | 0,18 €
minutos | Corte de pletinas laterales | 2 | 1,2 | 2,4 | 0,33 € | 0,79 €

Fabricación de la caja parte superior, la forma de esta caja se realizará por soldeo de paredes de pletinas de acero formando un habitáculo para ruedas dentadas, para fijar la carcasa inferior con la superior de soldará una pletina en el perímetor del borde superior para hacer de reborde, en este se realizarán 14 taladro de 8,5mm, orificio pasante. En la base existirá un tapón de llenado M6. Las paredes laterales contarán con unas perforaciones de semicírculos donde se apoyarán los rodamientos, también existirán una diferencia de altura respecto a la base de la pared para poder taladrar y roscar tornillos M8x10 , por cada semicircunferencia corresponden 2 taladros situados a mitad del diámetro de 100 y del diámetro exterior del rodamiento. Material usado: C45

Capítulo | 01
Código | Ud

N

Tiempo total
de la
operación

Precio
unidad Importe

Reductora

Descripción

Cantidad (Kg o
min)
minutos | Corte de pletinas posterior y delantera | 1 | 2 | 2 | 0,33 € | 0,66 €
minutos | Corte de pletina base | 1 | 1,8 | 1,8 | 0,33 € | 0,60 €
minutos | Corte de pletinas de reborde | 2 | 1 | 2 | 0,33 € | 0,66 €
minutos | Limpieza de rebabas | 1 | 4 | 4 | 0,33 € | 1,32 €
minutos | Trazado de circunferencias pletinas laterales 34 H7 | 1 | 3,5 | 3,5 | 0,33 € | 1,16 €
minutos | Trazado de taladros pletinas laterales M8 | 1 | 1,2 | 1,2 | 0,33 € | 0,40 €
minutos | Trazado de taladros pletina base | 1 | 1,25 | 1,25 | 0,33 € | 0,41 €
minutos | Trazado de taladros pletinas de reborde | 1 | 5 | 5 | 0,33 € | 1,65 €
minutos | Taladrado a ø5 para facilitar el taladrado de ø34 H7, siendo ø5 por cada mm tarda 0,10 minutos (25 mm de espesor) | 25 | 0,08 | 2 | 0,33 € | 0,66 €
minutos | Taladrado a ø15 para facilitar el fresado de ø34 H7 , siendo ø10 por cada mm tarda 0,13 minutos | 25 | 0,1 | 2,5 | 1,33 € | 3,33 €
minutos | Taladrado a ø25 para facilitar el taladrado de ø34 H7, siendo ø25 por cada mm tarda 0,17 minutos | 25 | 0,17 | 4,25 | 2,33 € | 9,91 €
minutos | Fresado y planear hasta dejar la pletina en espesor 14, donde se respetarán los rebordes semicirculares de diámetro 100 que conservará el mismo espesor que tenia la pletina orginal. 11mm se deben retirar, por cada mm de profundidad a lo largo de la pletina (358mmx85,5) tarda 2 minutos | 11 | 2 | 22 | 2,33 € | 51,28 €
minutos | Taladrado a ø5 para facilitar el taladrado de ø34 H7, siendo ø5 por cada mm tarda 0,10 minutos (25 mm de espesor) (la pletina opuesta) | 25 | 0,08 | 2 | 0,33 € | 0,66 €
minutos | Taladrado a ø15 para facilitar el fresado de ø34 H7 , siendo ø10 por cada mm tarda 0,13 minutos | 25 | 0,1 | 2,5 | 1,33 € | 3,33 €
minutos | Taladrado a ø25 para facilitar el taladrado de ø34 H7, siendo ø25 por cada mm tarda 0,17 minutos | 25 | 0,17 | 4,25 | 2,33 € | 9,91 €

Capítulo | 01
Código | Ud

N

Tiempo total
de la
operación

Precio
unidad Importe

Reductora

Descripción

Cantidad (Kg o
min)
minutos | Fresado y planear hasta dejar la pletina en espesor 14, donde se respetarán los rebordes semicirculares de diámetro 100 que conservará el mismo espesor que tenia la pletina orginal. 11mm se deben retirar, por cada mm de profundidad a lo largo de la pletina (358mmx85,5) tarda 2 minutos | 11 | 2 | 22 | 2,33 € | 51,28 €
minutos | Taladrado a ø5 para facilitar el taladrado de M12, siendo ø5 por cada mm tarda 0,10 minutos (25 mm de espesor) | 15 | 0,08 | 1,2 | 0,33 € | 0,40 €
minutos | Taladrado de tapón de vaciado M16 pletina base, 0,4 minutos el taladro | 1 | 0,4 | 0,4 | 2,33 € | 0,93 €
minutos | Realizar roscado con macho de roscar a M16 | 1 | 3 | 3 | 2,33 € | 6,99 €
minutos | Taladrado de pletinas de reborde, cada taladro tarda 0,36 minutos | 14 | 0,36 | 5,04 | 2,33 € | 11,75 €
minutos | Taladrado M8 para la fijación de las tapetas, 2 taladros por cada circunferencia. La longitud del taladrado es finita a 10mm | 4 | 0,09 | 0,36 | 2,33 € | 0,84 €
minutos | Realizar roscado con macho de roscar a M8 | 4 | 1,5 | 6 | 2,33 € | 13,98 €
minutos | Taladrado M8 para la fijación de las tapetas, (pletina opuesta) 2 taladros por cada circunferencia. La longitud del taladrado es finita a 10mm | 4 | 0,09 | 0,36 | 2,33 € | 0,84 €
minutos | Realizar roscado con macho de roscar a M8 | 4 | 1,5 | 6 | 2,33 € | 13,98 €
minutos | Proceso de soldadura en ángulo para las pletinas laterales, 1,3 minutos por unidad | 2 | 1,8 | 3,6 | 2,33 € | 8,39 €
minutos | Proceso de soldadura en ángulo en las paredes posterior y delantera, 0,45 minutos por unidad | 2 | 0,45 | 0,9 | 2,33 € | 2,10 €
minutos | Proceso de soldadura en ángulo para las pletinas de reborde 2,5 minutos el reborde entero. | 1 | 2,5 | 2,5 | 2,33 € | 5,83 €
minutos | Limpieza de escoria y cepillado | 1 | 2,5 | 2,5 | 2,33 € | 5,83 €
minutos | Comprobación de soldadura | 1 | 4 | 4 | 2,33 € | 9,32 €
minutos | Uso del grupo de soldadura | 1 | 7 | 7 | 2,33 € | 16,32 €

Capítulo | 01
Código | Ud

N

Tiempo total
de la
operación

Precio
unidad Importe

Reductora

Descripción

Cantidad (Kg o
min)
Tiempo total invertido en minutos | 188,46
Ud | horas
| 3,141
MO01 | horas | Oficial de 1ª Ferralista | 1 | 19,85 € | 62,35 €
Subtotal partida subcapítulo 01.5.1 (CD) | 275,35 €
| | | %Costes Indirectos (CI) | | 7%
| | | Total partida subcapítulo 01.5.1 | | 294,62 €
| | | Total partida subcapítulo 01.5 | | 617,36 €

### 01.6.0 Tornillería

Ud

Ud | Tornillo M6 x 18 | 14 | 0,25 € | 3,50 €
Ud | Tornillo M8 x16 | 16 | 0,15 € | 2,40 €
Ud | Tornillo tapón M16 x 12 | 2 | 1,13 € | 2,26 €
Subtotal partida subcapítulo 01.6 (CD) | 8,16 €
%Costes Indirectos (CI) | 7%
Total partida subcapítulo 01.6. | 8,73 €

### 01.6.1 Elementos de arrastre

Ud

Ud | Lengüeta plana tipo A 12x8x56 | 1 | 0,74 € | 0,74 €
Ud | Lengüeta plana tipo A 10x8x56 | 1 | 0,63 € | 0,63 €
Subtotal partida subcapítulo 01.6.1 (CD) | 1,37 €
%Costes Indirectos (CI) | 7%
Total partida subcapítulo 01.6.1 | 1,47 €

### 01.6.2 Rodamientos

Ud

Ud | Rodamiento rígido de bolas SKF 16007 | 2 | 11,73 € | 23,46 €
Ud | Rodamiento rígido de bolas SKF 16008 | 2 | 12,47 € | 24,93 €
Subtotal partida subcapítulo 01.6.2 (CD) | 48,40 €
%Costes Indirectos (CI) | 7%
Total partida subcapítulo 01.6.2 | 51,78 €

### 01.6.3 Retenes

Elementos que no se tienen que fabricar

Subcapítulo

Lista de elementos de uniones desmontables con precios de catálogo del fabricante norelem.

Subcapítulo

Lista de elementos de uniones desmontables con precios de catálogo del fabricante norelem.

Subcapítulo

Lista de rodamientos rígidos de bolas SKF necesario según precios del catálogo de norelem

Subcapítulo

Capítulo | 01
Código | Ud

N

Tiempo total
de la
operación

Precio
unidad Importe

Reductora

Descripción

Cantidad (Kg o
min)

Ud

Ud | Retén NBR 35x45x7 | 1 | 4,59 € | 4,59 €
Ud | Retén NBR 40x52x7 | 1 | 5,98 € | 5,98 €
Subtotal partida subcapítulo 01.6.3 (CD) | 10,57 €
%Costes Indirectos (CI) | 7%
Total partida subcapítulo 01.6.3 | 11,31 €

### 01.6.4 Elementos consumibles

Ud

l | Aceite ISO 100 para transmisión de ruedas dentadas | 1,75 | 2,49 € | 4,36 €
g | Sellador de estanqueidad de uniones | 110 | 0,12 € | 13,00 €
Kg | Lubricación elastohidrodinámica mylikote | 0,06 | 15,80 € | 0,95 €
Subtotal partida subcapítulo 01.6.4 (CD) | 17,36 €
%Costes Indirectos (CI) | 7%
Total partida subcapítulo 01.6.4 | 18,57 €
Total partida subcapítulo 01.6 | 91,86 €

### 01.7.0 Montaje de reductora

Ud

minutos | Estudiar plano de conjunto | 1 | 2 | 2 | 0,33 € | 0,66 €
minutos | Recoger , limpiar | 3 | 5,11 | 15,33 | 0,33 € | 5,06 €
minutos | Limpieza de la máquina | 1 | 15 | 15 | 0,33 € | 4,95 €
minutos | Preparación de herramientas necesarias | 1 | 0,35 | 0,35 | 0,33 € | 0,12 €
minutos | Comprobación final | 1 | 0,3 | 0,3 | 0,33 € | 0,10 €
minutos | Acople de la lengüeta en un árbol | 2 | 0,4 | 0,8 | 0,33 € | 0,26 €
minutos | Acople de rueda dentada en un árbol | 2 | 1 | 2 | 0,33 € | 0,66 €
minutos | Acople de rodamiento en un extremo de un árbol | 4 | 3 | 12 | 0,33 € | 3,97 €
minutos | Acople de casquillo en un extremo de un árbol | 4 | 0,55 | 2,2 | 0,33 € | 0,73 €
minutos | Colocación de una tapeta ciega sin tornillos | 2 | 1,2 | 2,4 | 0,33 € | 0,79 €
minutos | Colocación de 1 tornillo M8x16 en una tapeta ciega | 4 | 0,45 | 1,8 | 0,33 € | 0,60 €
minutos | Acople de un árbol montado en la caja inferior de la reductora | 2 | 0,5 | 1 | 0,33 € | 0,33 €

Montaje de reductora, contando con los distintos elementos descritos en el plano de conjunto.

Lista de rodamientos rígidos de bolas SKF necesario según precios del catálogo de norelem

Montaje

Subcapítulo

Subcapítulo

Lista de elementos consumibles necesarios

Capítulo | 01
Código | Ud

N

Tiempo total
de la
operación

Precio
unidad Importe

Reductora

Descripción

Cantidad (Kg o
min)
minutos | Colocación de una tapeta de entrada sin tornillos | 2 | 1,2 | 2,4 | 0,33 € | 0,79 €
minutos | Colocación de 1 tornillo M8x16 en una tapeta de entrada | 4 | 0,45 | 1,8 | 0,33 € | 0,60 €
minutos | Cierre de reductora mediante la caja superior sin tornillos | 4 | 0,45 | 1,8 | 0,33 € | 0,60 €
minutos | Colocación de 1 tornillo M8x16 (para los restantes) | 8 | 0,45 | 3,6 | 0,33 € | 1,19 €
minutos | Colocación de 1 tornillo M6x18 para fijar las cajas | 14 | 0,46 | 6,44 | 0,33 € | 2,13 €
minutos | Acople de 1 retén NBR | 2 | 0,52 | 1,04 | 0,33 € | 0,34 €
minutos | Colocación de 1 tapón de vaciado | 1 | 0,5 | 0,5 | 0,33 € | 0,17 €
minutos | Llenado de aceite a la caja reductora sellada, 1l aproximadamente 1 minuto (a llenar 2,85 l) | 2,85 | 1 | 2,85 | 0,33 € | 0,94 €
minutos | Colocación de 1 tapón de llenado | 1 | 0,5 | 0,5 | 0,33 € | 0,17 €
minutos | Por cada acople de caja y tapeta untar sellador | 5 | 0,56 | 2,8 | 0,33 € | 0,93 €
Tiempo total invertido en minutos | 78,91
Ud | horas
| 1,315
MO01 | horas | Oficial de 1ª Ferralista | 1 | 19,85 € | 26,11 €
| | | Subtotal partida subcapítulo 01.7 (CD) | | 26,85 €
| | | %Costes Indirectos (CI) | | 7%
| | | Total partida subcapítulo 01.7 | | 28,73 €
| | | Total partida subcapítulo 01.7 | | 28,73 €
| | | | | 1.486,77 €
| | | | | 1.564,06 €

Total Capítulo 1 sin contar 2 veces cada
casquillo
Total real capítulo 1

Presupuesto | Reductora
Capítulo | 01
Código | Ud | N | Importe

### 01.1.0 Piñón

E01 01 | Ud | Piñón | 1 | 85,26 €

### 01.1.1 Corona

E02 01 | Ud | Corona | 1 | 231,96 €

### 01.2.0 Árbol de transmisión de entrada

E02 01 | Ud | Árbol de transmisión de entrada | 1 | 67,68 €

### 01.2.1 Árbol de transmisión de salida

E02 01 | Ud | 1 | 73,06 €
Total partida 1.1 | 72,42 €
| Subcapítulo

Fabricación de una unidad de árbol que

Árbol de transmisión de salida | 73,06 €

67,68 €

Subtotal | 67,68 €
CI | 7%

Fabricación de una unidad de árbol que

CI | 7%
Total partida 1.1.1 | 248,20 €

Subcapítulo

Total partida | 339,43 €

Árboles de transmisión

Subcapítulo

231,96 €

Fabriación de una unidad de Corona con las características acorde a los planos de fabricación

Subtotal | 231,96 €

Reductora

Descripción | Cantidad Precio

Ruedas dentadas

Total partida 1.1.0 | 91,22 €

Fabricación de una unidad de piñón con las características acorde a los planos de fabricación

Subcapítulo

85,26 €

Subtotal | 85,26 €
CI | 7%
Mediciones, unidad de obra y presupuesto | 21/02/2021 | 5

Presupuesto | Reductora
Capítulo | 01 | Reductora

### 01.3.0 Tapeta árbol de entrada

E03 01 | Ud | 1 | 44,44 €

### 01.3.1 Tapeta ciega árbol de entrada

E03 01 | Ud | 1 | 40,46 €

### 01.3.2 Tapeta árbol de salida

E03 01 | Ud | 1 | 44,57 €

### 01.3.3 Tapeta ciega árbol de salida

E03 01 | Ud | 1 | 40,16 €
Total partida | 181,52 €
CI | 7%
Total partida 1.1 | 42,98 €
Tapeta ciega árbol de salida | 40,16 €

Fabricación de una unidad de tapeta ciega

Subtotal | 40,16 €
CI | 7%
Total partida 1.1 | 47,69 €

Subcapítulo

Tapeta árbol de salida | 44,57 €

Fabricación de una unidad de tapeta

Subtotal | 44,57 €
CI | 7%
Total partida 1.1 | 43,29 €

Subcapítulo

Tapeta ciega árbol de salida | 40,46 €

Fabricación de una unidad de tapeta ciega

Subtotal | 40,46 €
Total partida | 150,59 €

Tapetas

Tapeta árbol de entrada

Subcapítulo

CI | 7%
Total partida 1.1 | 47,55 €

Subcapítulo

44,44 €

Fabricación de una unidad de tapeta

Subtotal | 44,44 €
Subtotal | 73,06 €
CI | 7%
Total partida 1.1 | 78,18 €
Mediciones, unidad de obra y presupuesto | 21/02/2021 | 5

Presupuesto | Reductora
Capítulo | 01 | Reductora

### 01.4.0 Casquillo separador árbol de entrada

E04 01 | Ud | 2 | 71,17 €

### 01.4.1 Casquillo separador árbol de salida

E04 01 | Ud | 2 | 73,29 €

### 01.5.0 Caja de la reductora parte inferior

E05 01 | Ud | 1 | 301,62 €

### 01.5.1 Caja de la reductora parte superior

E05 01 | Ud | 1 | 275,35 €
Total partida | 617,36 €

Elementos que no se tienen que fabricar

Total partida 1.1 | 294,62 €
Total partida | 154,58 €

Fabricación de la caja de la reductora

Subtotal | 275,35 €
CI | 7%
Total partida 1.1 | 322,74 €

Subcapítulo

Caja de la reductora parte superior | 275,35 €

Fabricación de la caja de la reductora

Subtotal | 301,62 €
CI | 7%

Caja

Subcapítulo

Caja de la reductora parte inferior | 301,62 €
Subtotal | 73,29 €
CI | 7%
Total partida 1.1 | 78,42 €

Subcapítulo

Casquillo separador árbol de salida | 36,65 €

Fabricación de una unidad de casquillo

Subtotal | 71,17 €
CI | 7%
Total partida 1.1 | 76,15 €

Subcapítulo

Casquillo separador árbol de entrada | 35,59 €

Fabricación de una unidad de casquillo

Casquillos

Mediciones, unidad de obra y presupuesto | 21/02/2021 | 5

Presupuesto | Reductora
Capítulo | 01 | Reductora

### 01.6.0 Tornillería

E06 01 | Ud | 1 | 8,16 €

### 01.6.1 Elementos de arrastre

E06 01 | Ud | 1 | 1,37 €

### 01.6.2 Rodamientos

E06 01 | Ud | 1 | 48,40 €

### 01.6.3 Retenes

E06 01 | Ud | 1 | 10,57 €

### 01.6.4 Elementos consumibles

E06 01 | Ud | 1 | 17,36 €
CI | 7%
Total partida 1.1 | 18,57 €
Total partida | 91,86 €
Pack consumibles | 17,36 €

Conjunto de consumibles necesarios para

Subtotal | 17,36 €
CI | 7%
Total partida 1.1 | 11,31 €

Subcapítulo

Pack de retenes | 10,57 €

Conjunto de retenes necesarios para las

Subtotal | 10,57 €
CI | 7%
Total partida 1.1 | 51,78 €

Subcapítulo

Pack de 2 pares de rodamientos | 48,40 €

Conjunto de 2 pares de rodamientos SKF

Subtotal | 48,40 €
CI | 7%
Total partida 1.1 | 1,47 €

Subcapítulo

Pack lengüetas | 1,37 €

Conjunto de lengüetas Tipo A para el

Subtotal | 1,37 €
CI | 7%
Total partida 1.1 | 8,73 €

Subcapítulo

Pack Tornillería | 8,16 €

Conjunto de tornillería necesaria para el

Subtotal | 8,16 €

Subcapítulo

Mediciones, unidad de obra y presupuesto | 21/02/2021 | 5

Presupuesto | Reductora
Capítulo | 01 | Reductora

### 01.7.0 Montaje de la reductora

E07 01

Ud
1 26,85 €

Margen de
beneficios

20%

Subtotal con
márgen de
beneficios

Total presupuesto

IVA
2.271,01 €

21%

1.876,87 €

Total partida 1.1 | 28,73 €
Total partida | 28,73 €
Subtotal capítulo 1 | 1.564,06 €

Montaje completo de la reductora según

Subtotal | 26,85 €
CI | 7%

Montaje

Subcapítulo

Montaje completo de la reductora | 26,85 €
Mediciones, unidad de obra y presupuesto | 21/02/2021 | 5

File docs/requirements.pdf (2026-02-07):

PROYECTO REDUCTORA | 21 DE FEBRERO DE 2022


CARLOS LÓPEZ JIMÉNEZ | 48

# Proyecto Reductora de velocidad por engranajes

2º de Mecatrónica Industrial.

# Documento Nº6:

# Pliego de condiciones

Código PR-2

Autor: Carlos López Jiménez Fecha: 21/02/2022

CARLOS LÓPEZ JIMÉNEZ 49

## Índice

Capítulo II Condiciones generales | 51

### 1. Pliego de condiciones de índole facultativa | 51

### 1.1 CIF1 Obligaciones y derechos del Contratista | 51

### 1.1.1 Representación del contratista | 52

### 1.2 CIF2 Facultades del Director de Obra | 52

### 1.3. CIF3 Libro de Órdenes | 52

### 1.4 CIF4 Replanteo y preparación | 52

1.5 CIF5 Comienzo, ritmo, plazo y condiciones generales de ejecución de los trabajos. ... 53

### 1.6 CIF6 Control de calidad y ensayos. (ISO 9000) | 54

### 1.7 CIF7 Obras defectuosas y modificaciones por causa de fuerza mayor | 55

### 1.7.1 Prórroga por causa de fuerza mayor | 55

### 1.8 CIF8 Partidas Alzadas que figuren en el presupuesto | 55

### 1.9 CIF9 Periodo de prueba | 56

### 2. Pliego de condiciones generales de índole económica | 56

### 2.1 CIE1 Fianza | 56

### 2.2 CIE2 Composición de precios unitarios de ejecución y por contrata | 56

### 2.3 CIE3 Precios contradictorios o de partidas alzadas | 56

### 2.4 CIE4 Mejora y modificaciones de obra, instalaciones y máquinas | 56

### 2.5 CIE5 Revisión de precios | 57

### 2.6 CIE6 Valoración, medición y abono de trabajos | 57

### 2.7 CIE7 Penalizaciones | 57

### 2.8 CIE8 Seguros y conservación de las obras, maquinarias e instalaciones | 57

### 2.9 CIE9 Condiciones de pago de la maquinaria, equipos e instalaciones | 57

### 3. Condiciones generales de índole legal | 58

### 3.1 CIL1 Características del Contratista | 58

### 3.2 CIL2 Tipo de contrato | 58

### 3.3. CIL3 Tipo de adjudicación | 58

### 3.4. Arbitraje y jurisdicción competente | 59

### 3.5 CIL5 Responsabilidad del Contratista | 59

### 3.6 CIL7 Impuestos | 59

### 3.7 CIL8 Accidentes de trabajo | 59

### 3.8 CIL9 Causas de rescisión del contrato | 59

### 3.9 CIL10 Proceso de licitación | 59

Capítulo III: Condiciones particulares | 60

CARLOS LÓPEZ JIMÉNEZ 50

### 4. Condiciones específicas del proyecto | 60

### 4.1 CPI Condiciones del proyecto | 60

### 4.2 CP2 Condiciones particulares de la unidad de obra | 60

### 4.3 CP3 Condiciones particulares de materia prima | 60

CARLOS LÓPEZ JIMÉNEZ 51

Capítulo I. Descripción general del proyecto. Se ha realizado un proyecto para construir una reductora de velocidad, el objeto de construir esta máquina es complementar una etapa de funcionamiento de una paletizadora.

Esta máquina está formada por una etapa compuesta por dos pares de engranajes de dientes rectos. El cliente pide que se diseñe esta reductora bajo una serie de condiciones descritas en el Anexo de Cálculos y en la Memoria 2.1.4.2.

En caso de duda o algún detalle omitido o no suficientemente especificado en el presente Pliego de Condiciones ni en la documentación gráfica escrita del presente proyecto, bien sea esto por su obviedad o por su poca importancia, se aceptarán en la ejecución de las distintas unidades del proceso, las normas de la buena práctica teniendo siempre en cuenta la calidad como máxima.

Se expone, por tanto, la documentación necesaria que regirá toda la elaboración y fabricación del presente reductor de velocidad.

Como objetivo se tendrá fijar las condiciones de los materiales, de la ejecución, de su modificación, de la ejecución de las tolerancias, de su proceso de montaje, pruebas y las condiciones que se deben considerar a la hora de ensayar, las comprobaciones de las fases del montaje serán necesarias para la materialización del proyecto.

Capítulo II Condiciones generales

1. Pliego de condiciones de índole facultativa
1.1 CIF1 Obligaciones y derechos del Contratista. Las obligaciones del contratista son:
- Conocer las leyes.
- Conocer el proyecto en todos sus extremos.
- No proceder a realizar ninguna unidad de obra, sin la autorización del Director de Obra, a través de una orden vía Libro de Órdenes.
- Poner los medios necesarios para el desarrollo de las obras.

Los derechos son:

- Recibir una copia del proyecto.
- Recibir asistencia del Director de Obra, para solucionar los problemas técnicos que se planteen.
- Le sean suministrados los materiales y medios auxiliares de obra, si el contrato así lo estipula.

CARLOS LÓPEZ JIMÉNEZ 52

1.1.1 Representación del contratista
El fabricante está obligado a comunicar a la propiedad la persona designada como delegado suyo durante la fabricación, que tendrá carácter de jefe de esta, con dedicación plena y facultades para representarle y adoptar en todo momento cuantas decisiones competan a la contrata.

1.2 CIF2 Facultades del Director de Obra.
Corresponde al Ingeniero Técnico Director:
- Comprobar la adecuación de dicha reductora de velocidad con su motor correspondiente.
- Listar y redactar los complementos o rectificaciones del proyecto que se precisen.
- Deber de asistir las veces que sean necesarias para resolver las contingencias que se produzcan e impartir instrucciones y complementarias que sean precisas para conseguir la correcta solución mecánica.
- Coordinar la intervención en la fabricación de otros técnicos.
- Aprobar liquidación final, certificaciones, asesorar al promotor en el acto de la recepción.
- Redactar cuando se necesite el estudio de los sistemas adecuados de riesgos del trabajo en la fabricación y aprobar el plano de seguridad e higiene para la aplicación del mismo.
- Planificar el control económico y de calidad de la fabricación.
- Realizar o disponer las pruebas y ensayos de materiales, instalaciones y demás unidades de fabricación. Efectuar comprobaciones que resulten necesarias para asegurar la calidad de la fabricación de acuerdo con el proyecto y la normativa técnica aplicable.
1.3. CIF3 Libro de Órdenes.
Se tendrá un libro de órdenes donde se dé la constancia de la comunicación entre el Director de obra y el Contratista, al ser el instrumento a través del cual se dan las órdenes.

El libro tendrá tres hojas autocopiativas: La blanca para el contratista, la rosa para el Director y la amarilla para el colegio profesional.

1.4 CIF4 Replanteo y preparación.
La fabricación de la reductora atenderá a las características de funcionamiento indicadas por el cliente, una vez procesada esta información se estudia el emplazamiento de instalación, se estudia la mejor forma de fabricar un elemento para que cumpla esas características.

El Director de Obra supervisará el replanteo y este firmará el Acta de replanteo, entre el Director de Obra, la Propiedad y el contratista, estableciéndose la fecha base para comenzar la ejecución de las obras.

CARLOS LÓPEZ JIMÉNEZ 53

Una vez se conoce como va a ser procedimiento se asignan los equipos de trabajo y se organiza el trabajo para trabajare con la mayor eficiencia posible y se prepara el encargo de todos los materiales necesarios para la fabricación de esta.

1.5 CIF5 Comienzo, ritmo, plazo y condiciones generales de ejecución de los trabajos. Se fija un comienzo y un final, se planifican los plazos para cumplir los elementos de la reductora para así obtener el producto para la fecha acordada.

- La fecha de inicio será el 01/03/2022.
- La fecha de finalización será el 023/04/2022.

Se concretarán el número de etapas por departamentos, cada uno de ellos se encargarán de una parte del proyecto:

- Trato con el cliente – Relaciones públicas y Dpt. Administración.
- Cálculos – Dpt. Ingenieros Técnicos I.
- Planos – Dpt. Ingenieros Técnicos II.
- Fabricación – Dpt. Fabricación y gestión de máquinas.
- Presupuesto – Dpt. Presupuesto y Contabilidad.
- Desarrollo del documento del proyecto y unión de todos los documentos – Dpt. Administración II.

En total contamos con nueve etapas para completar el proyecto.

A continuación, se muestran los plazos de finalización de cada etapa (diagrama Gantt):

Etapa o
Fases | Descripción
Marzo | Abril
Semana
1 | 2 | 3 | 4 | 1 | 2 | 3 | 4
I. Acordar con el cliente y cerrar trato.

II. Organizar trabajo a los departamentos.

III. Replanteo del proyecto. IV. Desarrollo de cálculos.
V. Desarrollo de planos.
VI. Fabricación de elementos de la reductora.

VII. Realización del presupuesto.

VIII. Desarrollo del documento del proyecto.

IX. Firma entre interesados

CARLOS LÓPEZ JIMÉNEZ 54

Obligatoriamente y por escrito el Contratista deberá dar cuenta al Ingeniero Técnico Director del comienzo de los trabajos al menos con tres días de antelación.

1.6 CIF6 Control de calidad y ensayos. (ISO 9000).
Los controles de calidad serán realizados según sean fabricados o comprados, uno por el director de fabricación y jefe de taller y otro por el sub director ingeniero respectivamente.

El director de obra deberá asistir a las muestras o ensayos realizados, si bien este no puede asistir se delegará este papel al sub director ingeniero.

Se especifican en la siguiente tabla los elementos necesarios para hacer la reductora, sus materiales y el modo de control de calidad:

Elemento | Material | Control de calidad | Norma
Ruedas dentadas | 37Cr4 | Control y comprobación por Director de fabricación
Tapetas | C45 | Control y comprobación por Director de fabricación
Casquillos | 1998 CC493K | Control y comprobación por Director de fabricación
Árboles de transmisión | 37CrMo4 | Control y comprobación por Director de fabricación
Caja | C45 | Control y comprobación por Director de fabricación
Rodamientos SKF | 100CrMo7 | Selección y comprobación por Sub Director Ingeniero | ISO 15
Retenes | NBR | Selección y comprobación por Sub Director Ingeniero | ISO 6194/1
Tornillos M8 x 16 | Acero | Selección y comprobación por | ISO 4762

CARLOS LÓPEZ JIMÉNEZ 55

| | Sub Director Ingeniero
Tornillos M6 x 18 | Acero | Selección y comprobación por Sub Director Ingeniero | ISO 4762
Lengüetas tipo A | C45EC | Selección y comprobación por Sub Director Ingeniero | ISO 773
Tornillo tapón M16 x 12 | Acero Cincado | Selección y comprobación por Sub Director Ingeniero | DIN 910

1.7 CIF7 Obras defectuosas y modificaciones por causa de fuerza mayor.
Si el contratista efectúa obras que resultan ser defectuosas, correrán a su cargo la subsanación de dichos defectos o vicios ocultos durante el periodo de garantía, o cuando así lo estime el Director del proyecto. Para obligar al Contratista sele impone una fianza que devolverá hasta que dicho periodo concluya.

El Contratista debe emplear materiales que cumplan con las condiciones exigidas en las Condiciones generales y Particulares de Índole Técnica de pliego de condiciones y realizará todos y cada uno de los trabajos contratados de acuerdo con lo especificado.

1.7.1 Prórroga por causa de fuerza mayor.
Si por causa de fuerza mayor o que sea independiente de la voluntad del fabricante y este no pudiese comenzar las tareas o tuviese que suspenderlas, o no le fuera posible terminarlas en los plazos prefijados, se le otorgará una prórroga para que la contrata cumpla el previo informe favorable del Ingeniero Técnico Director.

1.8 CIF8 Partidas Alzadas que figuren en el presupuesto.
Es de obligado cumplimiento de la contrata el realizar una buena realización de encargos demandados por el cliente. Punto aparte si el cliente desea realizar un cambio una vez ya realizado y aceptado el presupuesto estos correrán a su cuenta, en el caso contrario o en cuestiones de defectos de fabricación la contrata correrá a cargo de los gastos que no cuadren en el presupuesto. En los casos en los que no se haya contado algún elemento por no haber tenido suficiente información, es decir surge de improvisto para ambas partes, se deberá llegar a un acuerdo entre partes y si es necesario será arbitrado por una entidad externa.

Se entenderá que se requiere una reforma de proyecto con consentimiento expreso de la propiedad, toda variación que suponga incremento de precios de alguna unidad de fabricación en más del 20%, en el caso del total si es más de un 10%.

CARLOS LÓPEZ JIMÉNEZ 56

1.9 CIF9 Periodo de prueba.
Se corresponderán 15 días de prueba para que el cliente pruebe si se cumplen sus expectativas. Si no se cumplen las expectativas acordadas el fabricante será el responsable de dar una solución que complazca al cliente.

No se procederá a lo mencionado anteriormente si el cliente ha modificado, desmontado, dañado o alguna acción que haga que la reductora no funcione correctamente.
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

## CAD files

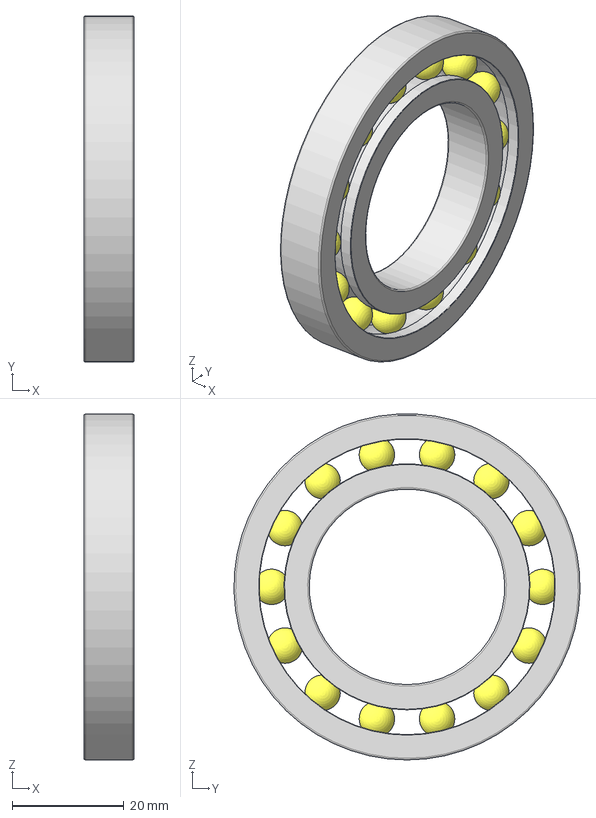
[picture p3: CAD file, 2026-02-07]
cad/Árbol 1/Rodamiento 16007/SKF_16007.stp
9.00 x 62.0 x 62.0 mm
_SKF_16007_PART1
_SKF_16007_PART2
_SKF_16007_PART3 x 14
_SKF_16007_PART4 x 14

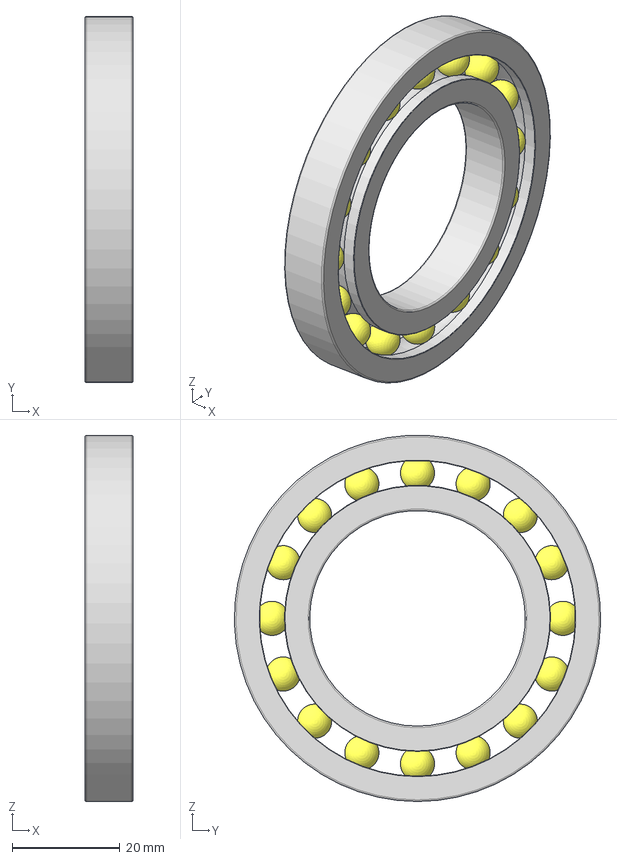
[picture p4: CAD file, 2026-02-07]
cad/Árbol 2/Rodamiento 16008/SKF_16008.stp
9.00 x 68.0 x 67.9 mm
_SKF_16008_PART1
_SKF_16008_PART2
_SKF_16008_PART3 x 16
_SKF_16008_PART4 x 16

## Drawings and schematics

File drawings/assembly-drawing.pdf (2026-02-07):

PROYECTO REDUCTORA | 21 DE FEBRERO DE 2022


CARLOS LÓPEZ JIMÉNEZ | 62

## Proyecto Reductora de velocidad por engranajes

2º de Mecatrónica Industrial.

# Planos

Código PR-6

Autor: Carlos López Jiménez Fecha: 21/02/2022

A

A

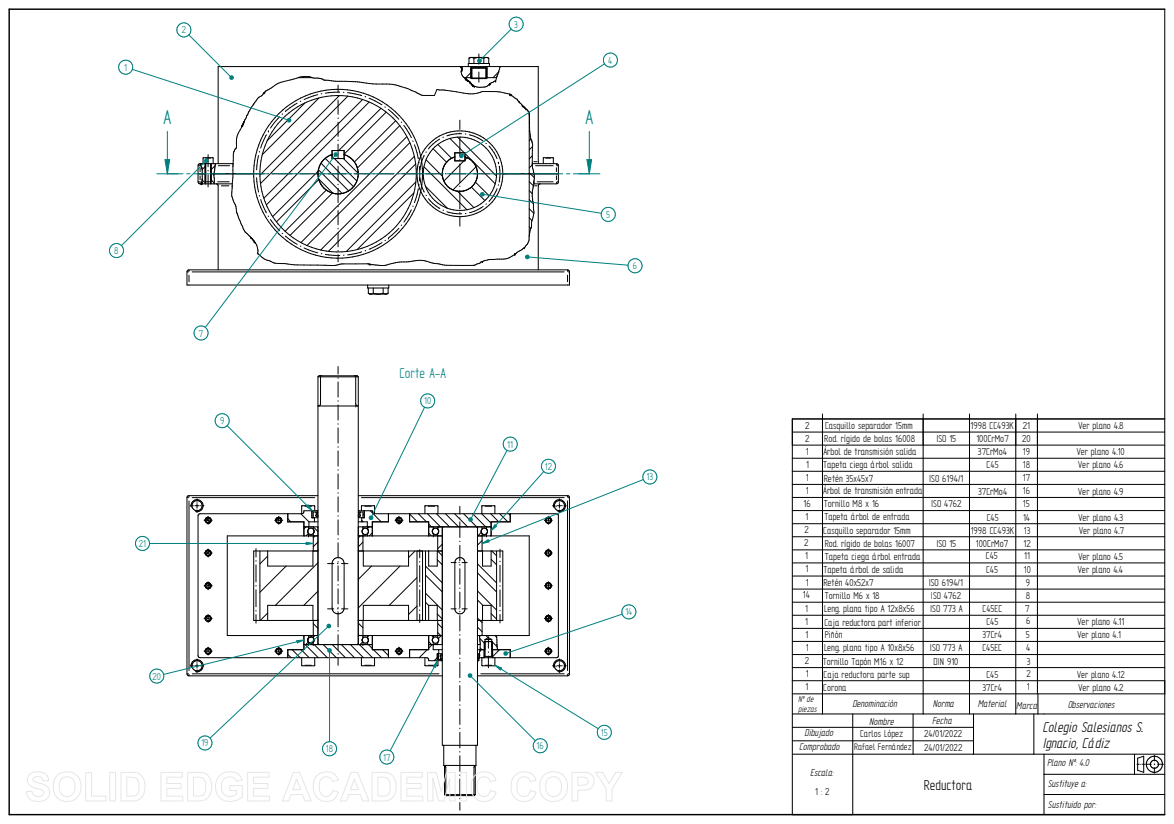
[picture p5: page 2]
Sustituye a:; Sustituido por:; Corte A-A

2 | Casquillo separador 15mm | | 1998 CC493K | 21 | Ver plano 4.8
2 | Rod. rígido de bolas 16008 | ISO 15 | 100CrMo7 | 20
1 | Árbol de transmisión salida | | 37CrMo4 | 19 | Ver plano 4.10
1 | Tapeta ciega árbol salida | | C45 | 18 | Ver plano 4.6
1 | Retén 35x45x7 | ISO 6194/1 | | 17
1 | Árbol de transmisión entrada | | 37CrMo4 | 16 | Ver plano 4.9
16 | Tornillo M8 x 16 | ISO 4762 | | 15
1 | Tapeta árbol de entrada | | C45 | 14 | Ver plano 4.3
2 | Casquillo separador 15mm | | 1998 CC493K | 13 | Ver plano 4.7
2 | Rod. rígido de bolas 16007 | ISO 15 | 100CrMo7 | 12
1 | Tapeta ciega árbol entrada | | C45 | 11 | Ver plano 4.5
1 | Tapeta árbol de salida | | C45 | 10 | Ver plano 4.4
1 | Retén 40x52x7 | ISO 6194/1 | | 9
14 | Tornillo M6 x 18 | ISO 4762 | | 8
1 | Leng. plana tipo A 12x8x56 | ISO 773 A | C45EC | 7
1 | Caja reductora part inferior | | C45 | 6 | Ver plano 4.11
1 | Piñón | | 37Cr4 | 5 | Ver plano 4.1
1 | Leng. plana tipo A 10x8x56 | ISO 773 A | C45EC | 4
2 | Tornillo Tapón M16 x 12 | DIN 910 | | 3

Caja reductora parte sup

C45 | 2 | Ver plano 4.12

1 | Corona | | 37Cr4 | 1 | Ver plano 4.2
Nº de piezas | Denominación | Norma | Material | Marca | Observaciones

Nombre | Fecha | | Colegio Salesianos S. Ignacio, Cádiz

Dibujado | Carlos López | 24/01/2022
Comprobado | Rafael Fernández | 24/01/2022
Escala: 1 : 2 | Reductora | Plano Nº: 4.0

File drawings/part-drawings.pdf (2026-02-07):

( | )
N8 | N7

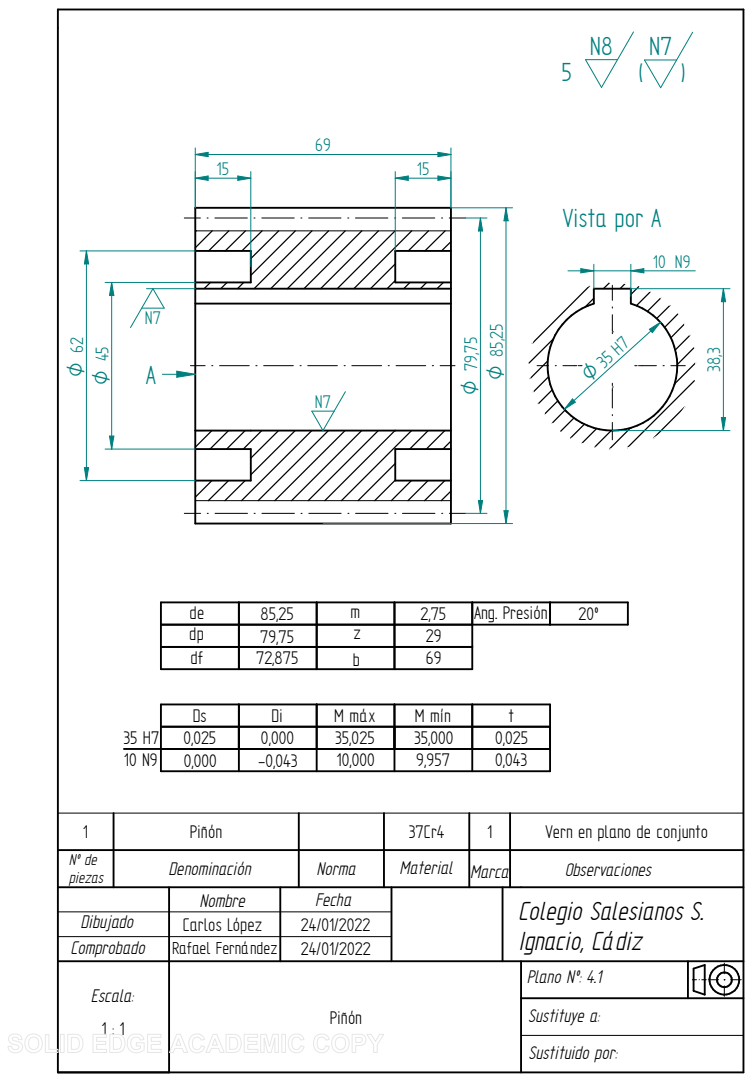
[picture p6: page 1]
Sustituye a:; Sustituido por:; Piñón; Vern en plano de conjunto ⁸⁵,25; Vista por A

de | 85,25 | m | 2,75 | Ang. Presión | 20º
dp | 79,75 | z | 29
df | 72,875 | b | 69

Ds | Di | M máx | M mín | t
0,025 | 0,000 | 35,025 | 35,000

Nº de piezas | Denominación | Norma | Material | Marca | Observaciones

Nombre | Fecha | | Colegio Salesianos S. Ignacio, Cádiz

Dibujado | Carlos López | 24/01/2022
Comprobado | Rafael Fernández | 24/01/2022
Escala: | Piñón | Plano Nº: 4.1

( | )
N8 | N7

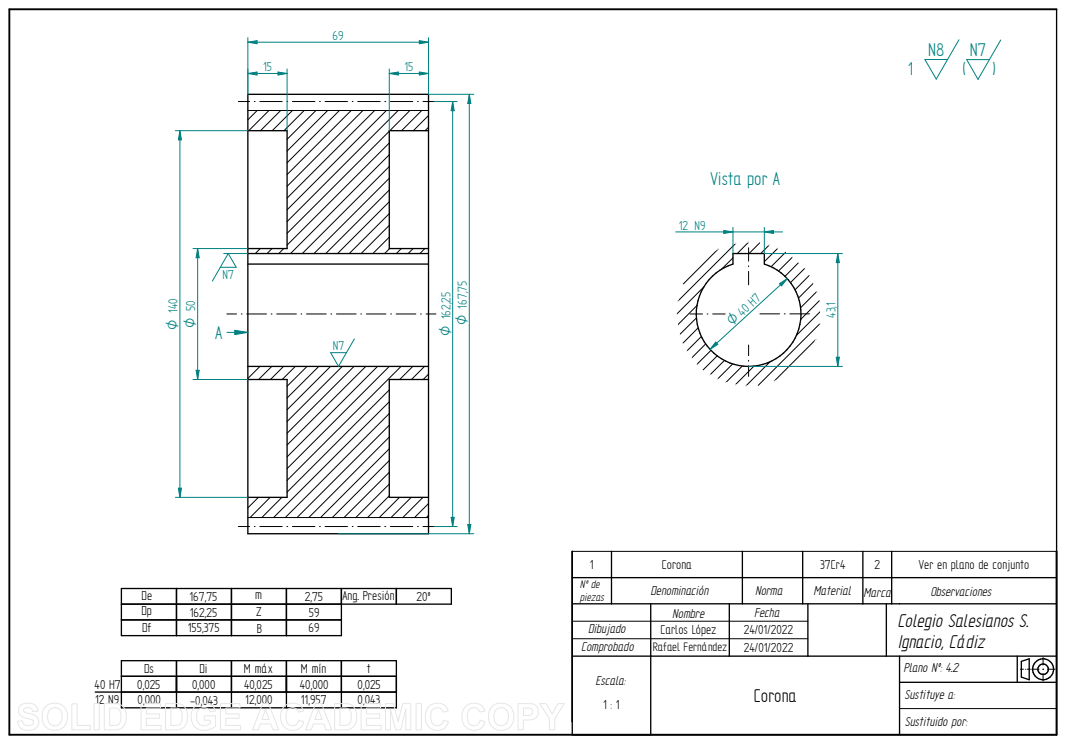
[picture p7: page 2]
Colegio Salesianos S. Ignacio, Cádiz; Sustituye a:; Nombre; Fecha; Dibujado; Carlos López; Vista por A

1 | Corona | | 37Cr4 | 2 | Ver en plano de conjunto
Nº de piezas | Denominación | Norma | Material | Marca | Observaciones

De | 167,75 | m | 2,75 | Ang. Presión | 20º

Comprobado | Rafael Fernández | 24/01/2022
Escala: | Corona | Plano Nº: 4.2

Ds | Di | M máx | M mín | t
0,025 | 0,000 | 40,025 | 40,000

( )

14

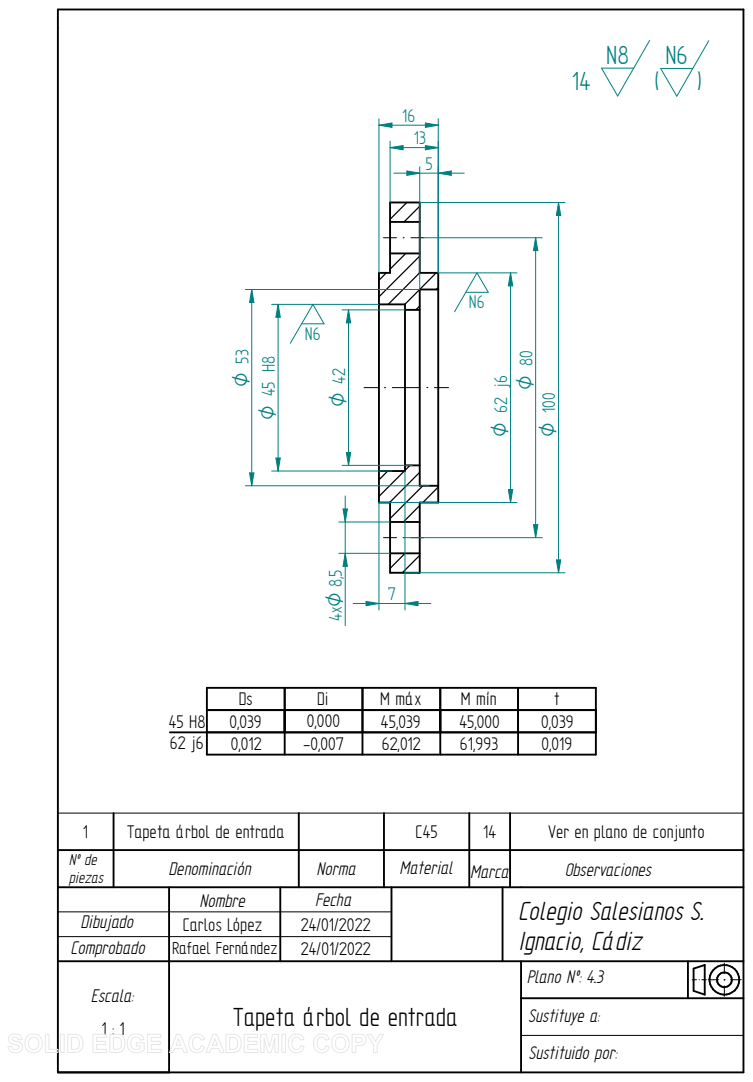
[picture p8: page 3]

Ds | Di | M máx | M mín | t
0,039 | 0,000 | 45,039 | 45,000

1 | Tapeta árbol de entrada | | C45 | 14 | Ver en plano de conjunto
Nº de piezas | Denominación | Norma | Material | Marca | Observaciones

Nombre | Fecha | | Colegio Salesianos S. Ignacio, Cádiz

Dibujado | Carlos López | 24/01/2022
Comprobado | Rafael Fernández | 24/01/2022
Escala: | Tapeta árbol de entrada | Plano Nº: 4.3

( )

10

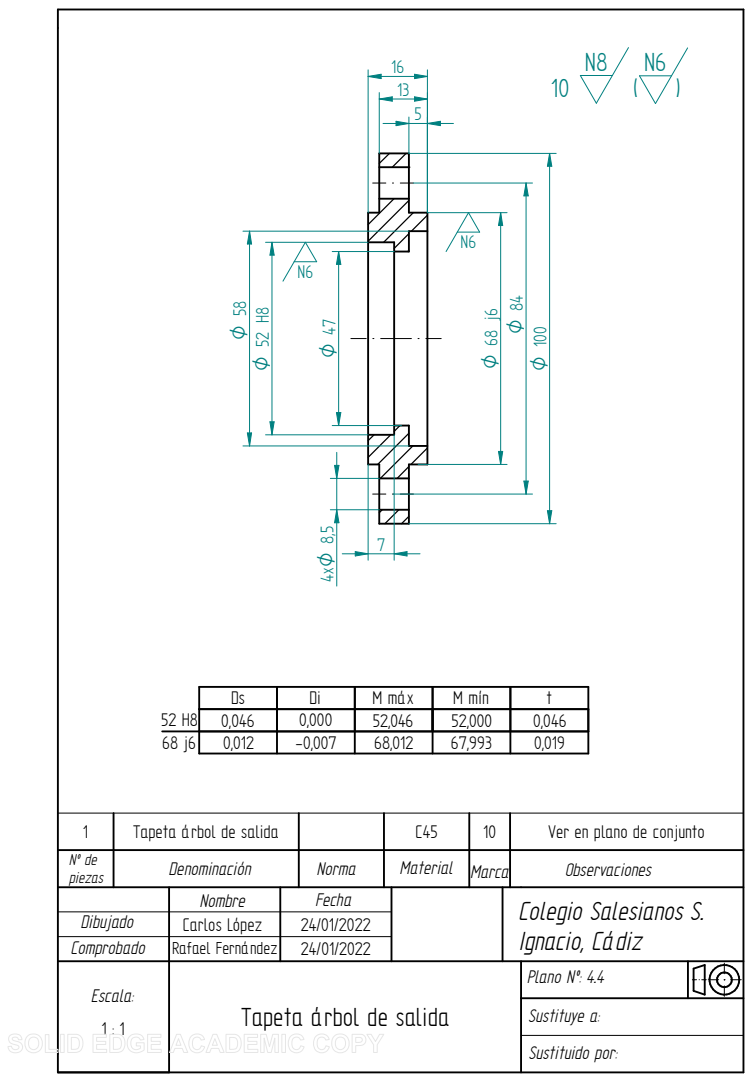
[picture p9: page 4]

Ds | Di | M máx | M mín | t
0,046 | 0,000 | 52,046 | 52,000

1 | Tapeta árbol de salida | | C45 | 10 | Ver en plano de conjunto
Nº de piezas | Denominación | Norma | Material | Marca | Observaciones

Nombre | Fecha | | Colegio Salesianos S. Ignacio, Cádiz

Dibujado | Carlos López | 24/01/2022
Comprobado | Rafael Fernández | 24/01/2022
Escala: | Tapeta árbol de salida | Plano Nº: 4.4

( )

11

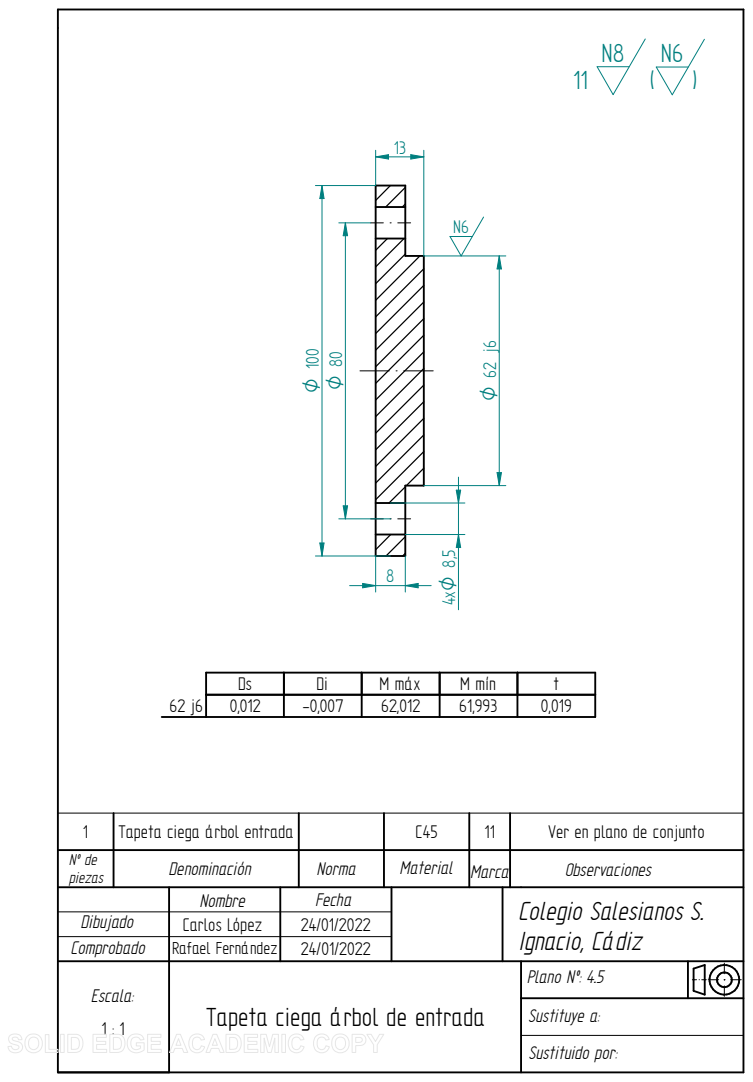
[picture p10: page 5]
M máx; M mín

1 | Tapeta ciega árbol entrada | | C45 | 11 | Ver en plano de conjunto
Nº de piezas | Denominación | Norma | Material | Marca | Observaciones

Nombre | Fecha | | Colegio Salesianos S. Ignacio, Cádiz

Dibujado | Carlos López | 24/01/2022
Comprobado | Rafael Fernández | 24/01/2022
Escala: | Tapeta ciega árbol de entrada | Plano Nº: 4.5

( )

18

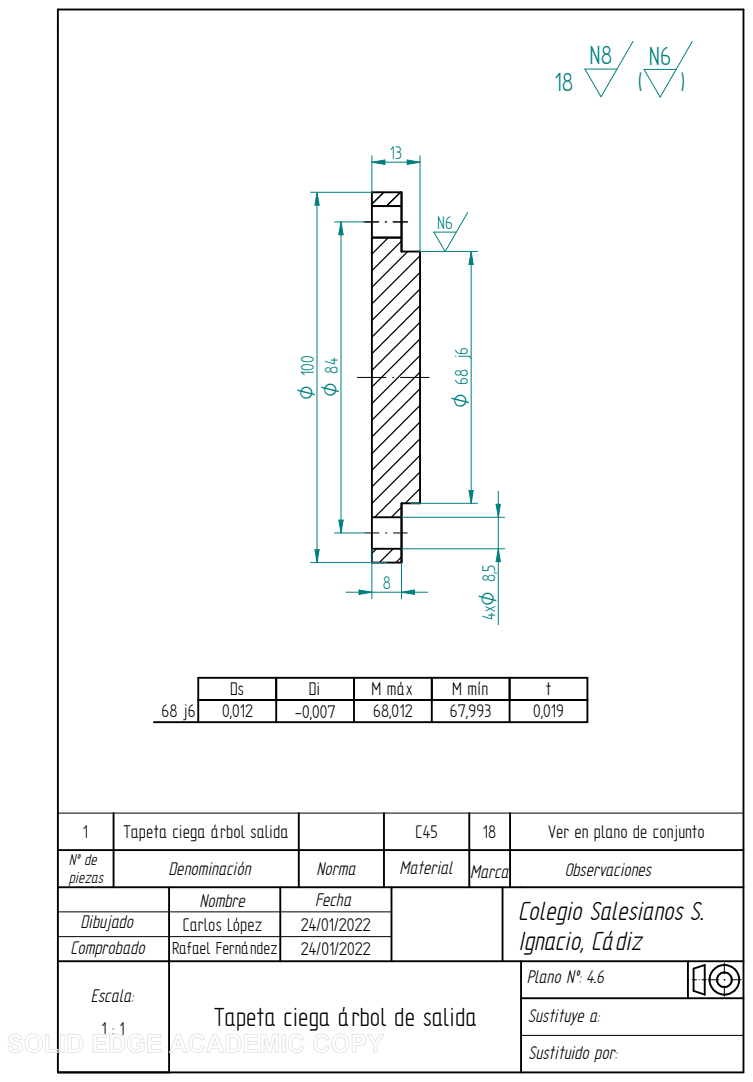
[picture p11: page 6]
M máx; M mín

1 | Tapeta ciega árbol salida | | C45 | 18 | Ver en plano de conjunto
Nº de piezas | Denominación | Norma | Material | Marca | Observaciones

Nombre | Fecha | | Colegio Salesianos S. Ignacio, Cádiz

Dibujado | Carlos López | 24/01/2022
Comprobado | Rafael Fernández | 24/01/2022
Escala: | Tapeta ciega árbol de salida | Plano Nº: 4.6

( )

13

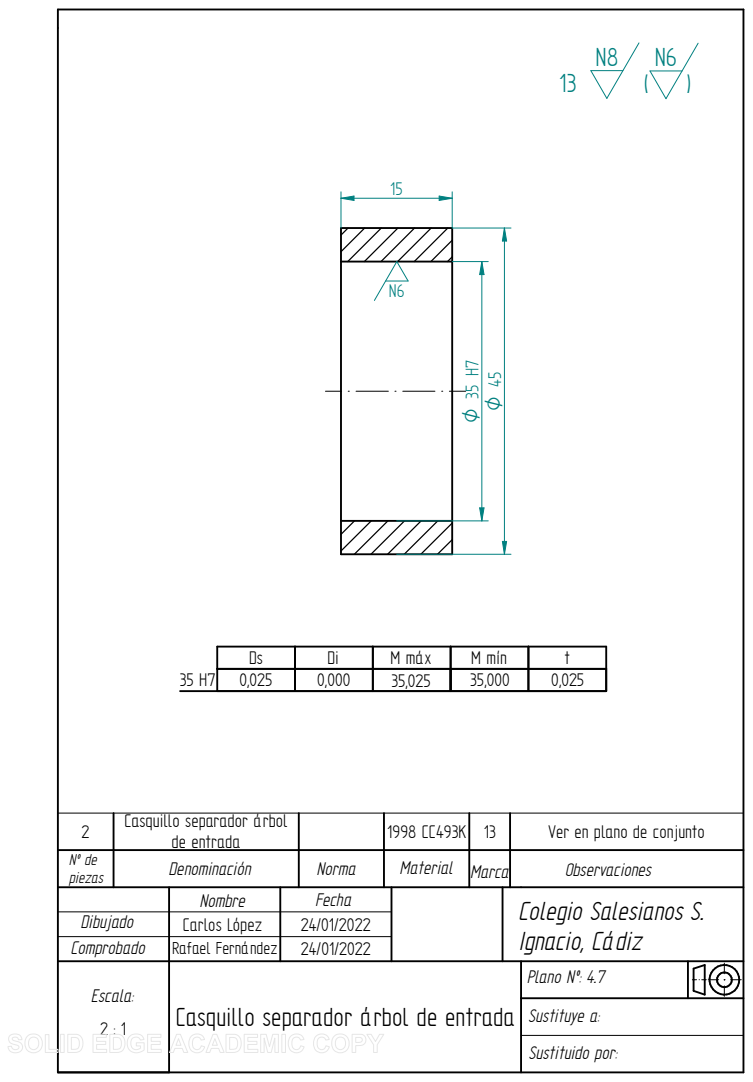
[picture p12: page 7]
M máx 35,025; M mín 35,000

Casquillo separador árbol de entrada⁴⁵

2 | Casquillo separador árbol de entrada | | 1998 CC493K | 13 | Ver en plano de conjunto

Nº de piezas | Denominación | Norma | Material | Marca | Observaciones

Nombre | Fecha | | Colegio Salesianos S. Ignacio, Cádiz

Dibujado | Carlos López | 24/01/2022
Comprobado | Rafael Fernández | 24/01/2022
Escala: | | Plano Nº: 4.7

( )

21

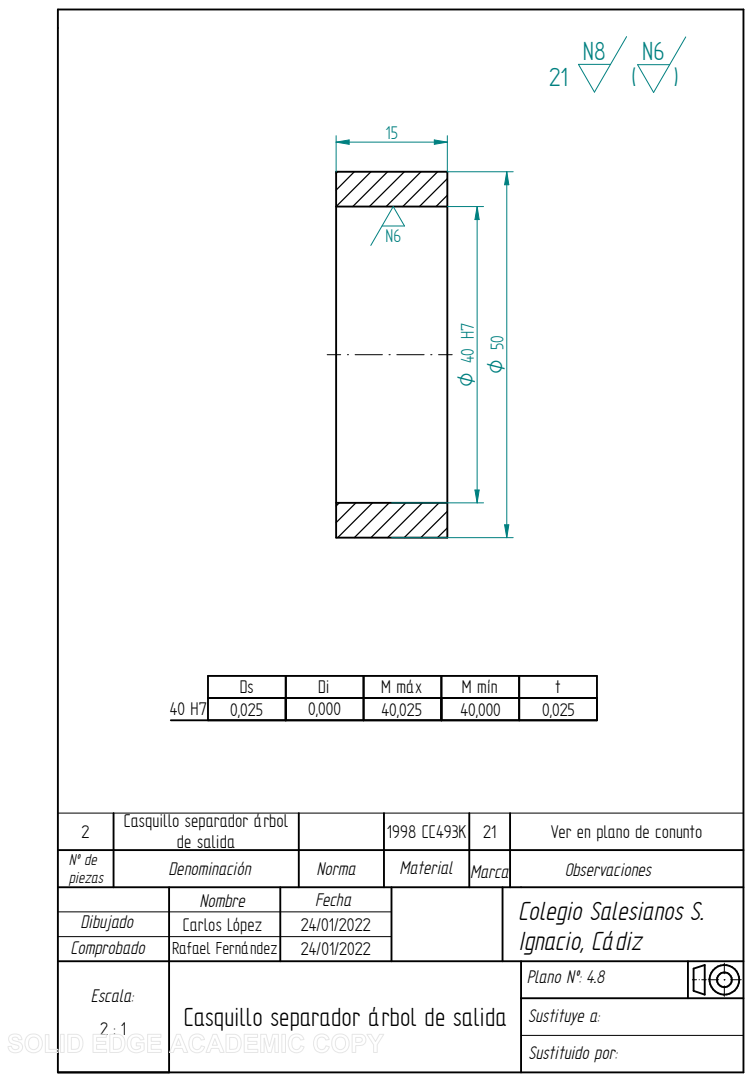
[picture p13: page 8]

Ds | Di | M máx | M mín | t
0,025 | 0,000 | 40,025 | 40,000

2 | Casquillo separador árbol de salida | | 1998 CC493K | 21 | Ver en plano de conunto

Nº de piezas | Denominación | Norma | Material | Marca | Observaciones

Nombre | Fecha | | Colegio Salesianos S. Ignacio, Cádiz

Dibujado | Carlos López | 24/01/2022
Comprobado | Rafael Fernández | 24/01/2022
Escala: | Casquillo separador árbol de salida | Plano Nº: 4.8

A

A

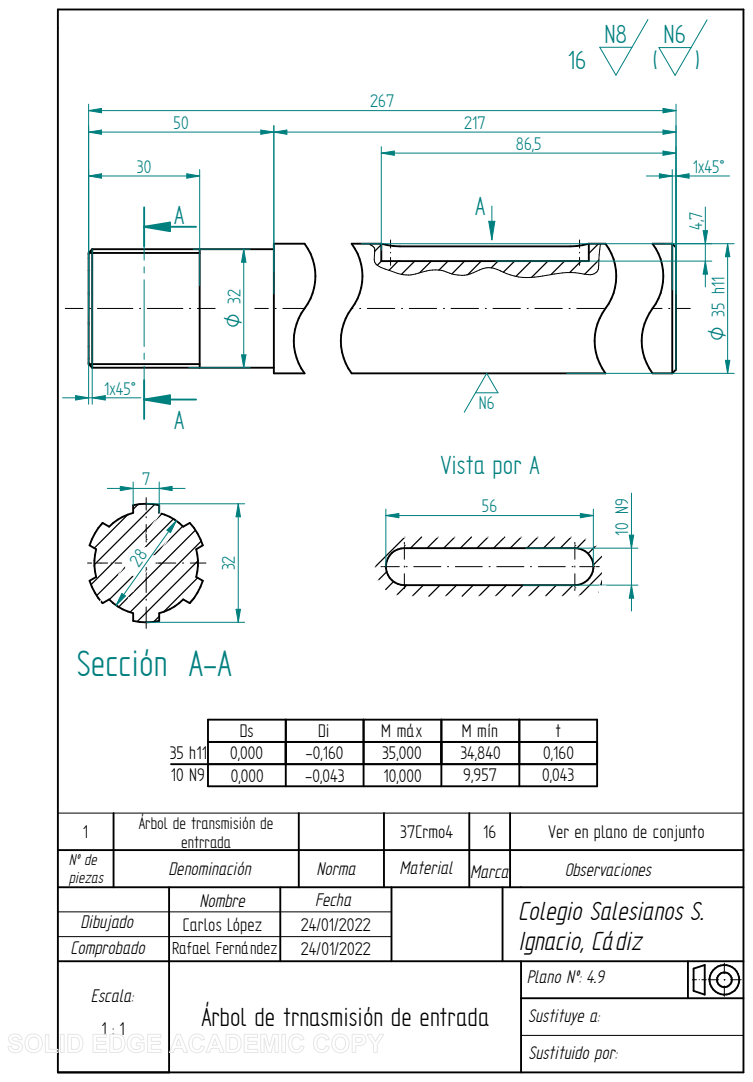
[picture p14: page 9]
Sección A-A; Vista por A

Ds | Di | M máx | M mín | t
0,000 | -0,160 | 35,000 | 34,840

1 | Árbol de transmisión de entrrada | | 37Crmo4 | 16 | Ver en plano de conjunto

Nº de piezas | Denominación | Norma | Material | Marca | Observaciones

Nombre | Fecha | | Colegio Salesianos S. Ignacio, Cádiz

Dibujado | Carlos López | 24/01/2022
Comprobado | Rafael Fernández | 24/01/2022
Escala: | Árbol de trnasmisión de entrada | Plano Nº: 4.9

( )

A

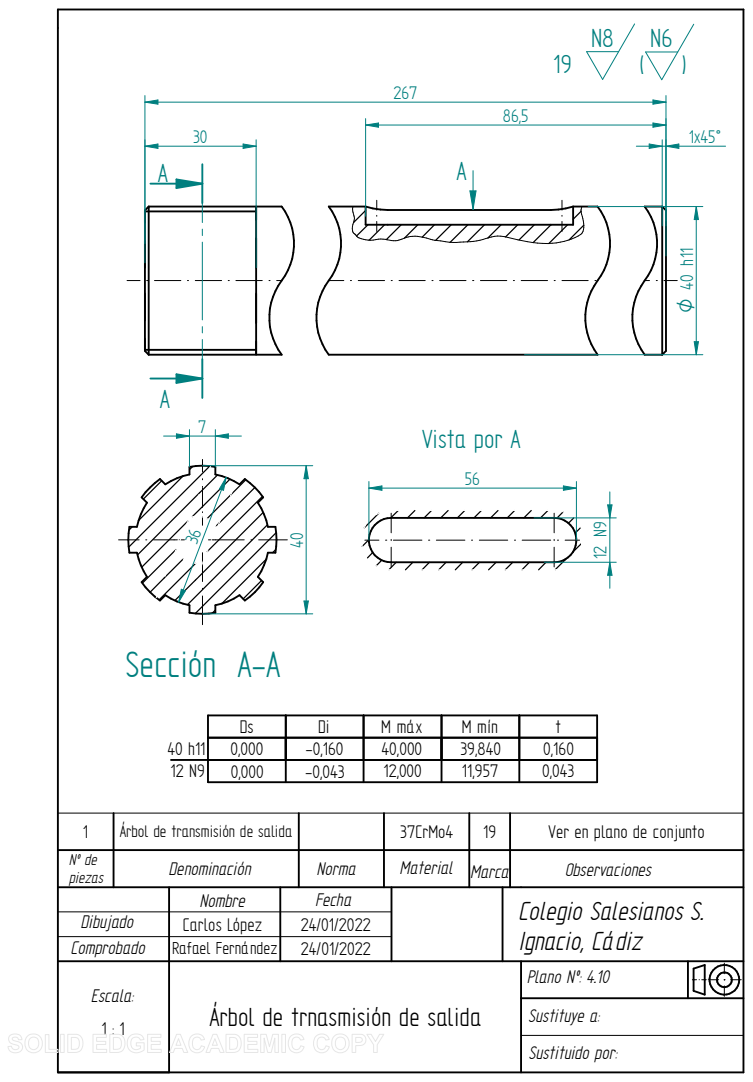
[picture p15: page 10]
Vista por A; Sección A-A

Ds | Di | M máx | M mín | t
0,000 | -0,160 | 40,000 | 39,840

1 | Árbol de transmisión de salida | | 37CrMo4 | 19 | Ver en plano de conjunto
Nº de piezas | Denominación | Norma | Material | Marca | Observaciones

Nombre | Fecha | | Colegio Salesianos S. Ignacio, Cádiz

Dibujado | Carlos López | 24/01/2022
Comprobado | Rafael Fernández | 24/01/2022
Escala: | Árbol de trnasmisión de salida | Plano Nº: 4.10
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

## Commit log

2026-02-03 Create cad directory
2026-02-04 Transmission ratio, output speed, output torque added.
2026-02-07 calculations, budget, design report, assembly dawing, part drawing added.
2026-02-07 parts and assembly added
    [Conjunto simplificado.cfg, Conjunto.cfg, SKF_16007.cfg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]

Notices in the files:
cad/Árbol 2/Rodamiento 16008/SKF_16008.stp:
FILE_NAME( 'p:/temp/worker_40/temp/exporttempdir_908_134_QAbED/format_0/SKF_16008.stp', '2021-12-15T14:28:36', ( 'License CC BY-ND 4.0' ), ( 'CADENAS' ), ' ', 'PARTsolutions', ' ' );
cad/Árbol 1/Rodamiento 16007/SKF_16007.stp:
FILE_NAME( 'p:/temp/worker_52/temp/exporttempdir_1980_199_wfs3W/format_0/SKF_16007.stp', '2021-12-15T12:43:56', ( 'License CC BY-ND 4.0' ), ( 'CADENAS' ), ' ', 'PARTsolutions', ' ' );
